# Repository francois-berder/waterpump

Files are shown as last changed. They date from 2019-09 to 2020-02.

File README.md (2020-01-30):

# Waterpump

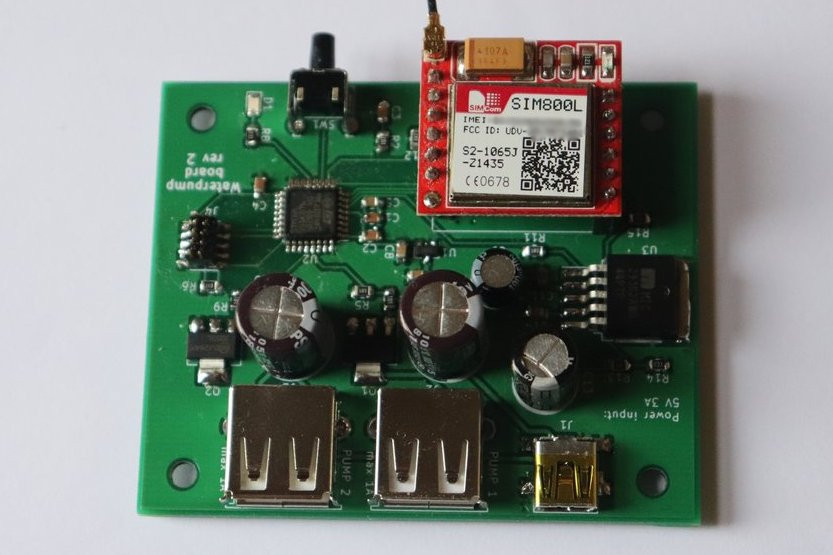
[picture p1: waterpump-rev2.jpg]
waterpump board Waterpump board rev 2


This project is an automatic system for watering plants. Everyday, pumps are switched on for a few seconds to provide enough water to some plants. The device can be controlled by sending SMS to change the schedule or water plants. In addition, a small push-button is present to water plants immediately.

## Build and flash instructions

### Prerequisites

You need to install the [ARM embedded toolchain](https://developer.arm.com/tools-and-software/open-source-software/developer-tools/gnu-toolchain/gnu-rm) and [JLink Software and Documentation Pack](https://www.segger.com/downloads/jlink/#J-LinkSoftwareAndDocumentationPack).

### SIM card configuration

The SIM card might need to be unlocked. The default PIN is set to 1234 by the `SIMCARD_PIN` macro that can be overriden.

To retrieve time from network, the firmware needs the APN name which depends on your
network provider. The macro `SIM800_APN_NAME` is currently set to `"free"` in the Makefile because I am using a SIM card from Free Mobile. Feel free to change it.

### Commands

There are two types of build: release and debug.

To build the project, run one of these commands:
```
$ make                  # BUILDTYPE set to release
$ BUILDTYPE=release make
$ BUILDTYPE=debug make
```

Connect the board to a SEGGER debug probe and run these commands to flash or debug the firmware:
```
$ make flash-target                 # Flash release firmware
$ BUILDTYPE=debug make flash-target # Flash debug firmware
$ BUILDTYPE=debug make debug-target # Start debugging firmware
```

## Building hardware

In `hardware` folder, there are Gerber files sent to [JLCPCB](https://jlcpcb.com/) for each revision of the board. I recommend that you build the latest revision of the board. Components can be bought on [RS online](https://uk.rs-online.com/web/).

### Issues with rev1 board

  * SIM800L Footprint is incorrect
  * No mounting holes
  * micro USB connector is too far away from the side of the board
  * Power circuit for SIM800L is not working properly. Large polarized capacitors are missing on the input and output of the LDO voltage regulator. The regulator is not able to handle load transients fast enough, causing the SIM800L to brown out.

### Issues with rev2 board

  * SIM800L footprint is still incorrect ! Although it is easier to insert the module in pin headers than on rev1.
  * micro USB connector should be replaced by a barrel connector because USB cables should not be used to provide 3A.

## Power requirements

The GSM module can use up to 2A and each pump should not use more than 1A due to the choice of MOSFET transistors (especially on rev 2).
For this reason, I recommend powering this board with a 5V 3A power supply. Alternatively if you are using only 2.5W pumps, a 5V 2.5A can be used.

## Switching on water pump

Both pumps are switched on in sequence for 3 seconds each if the push button is pressed or if the GSM modules receives a text message starting with "WATER ALL". If you only want to enable pump 1 or 2, send text message "WATER 1" or "WATER 2".

## SMS commands

| Command | description | examples |
| --- | --- | --- |
| `BUTTON <duration>` | Configure for how long each pump is enabled when button is pressed | `BUTTON 5` |
| `WATER <pump_index>` | Turn on one pump for `DEFAULT_PUMP_DURATION` seconds (default: 3s) | `WATER 1`, `WATER 2` |
| `WATER ALL` | Turn on both pumps, each for `DEFAULT_PUMP_DURATION` seconds (default: 3s)| `WATER ALL` |
| `SCHEDULE <index> STOP` | Disable a schedule| `SCHEDULE 0 STOP`, `SCHEDULE 1 STOP` |
| `SCHEDULE <index> <hour>:<min>:<sec> <duration> ALL` | Turn on both pumps once per day | `SCHEDULE 0 19:04:57 3 ALL` |
| `SCHEDULE <index> <hour>:<min>:<sec> <duration> <pump_index>` | Turn on a pump once per day | `SCHEDULE 2 06:43:00 7 1`, `SCHEDULE 3 06:43:00 9 2` |
| `SCHEDULE STATUS` | Request schedule status | `SCHEDULE STATUS` |

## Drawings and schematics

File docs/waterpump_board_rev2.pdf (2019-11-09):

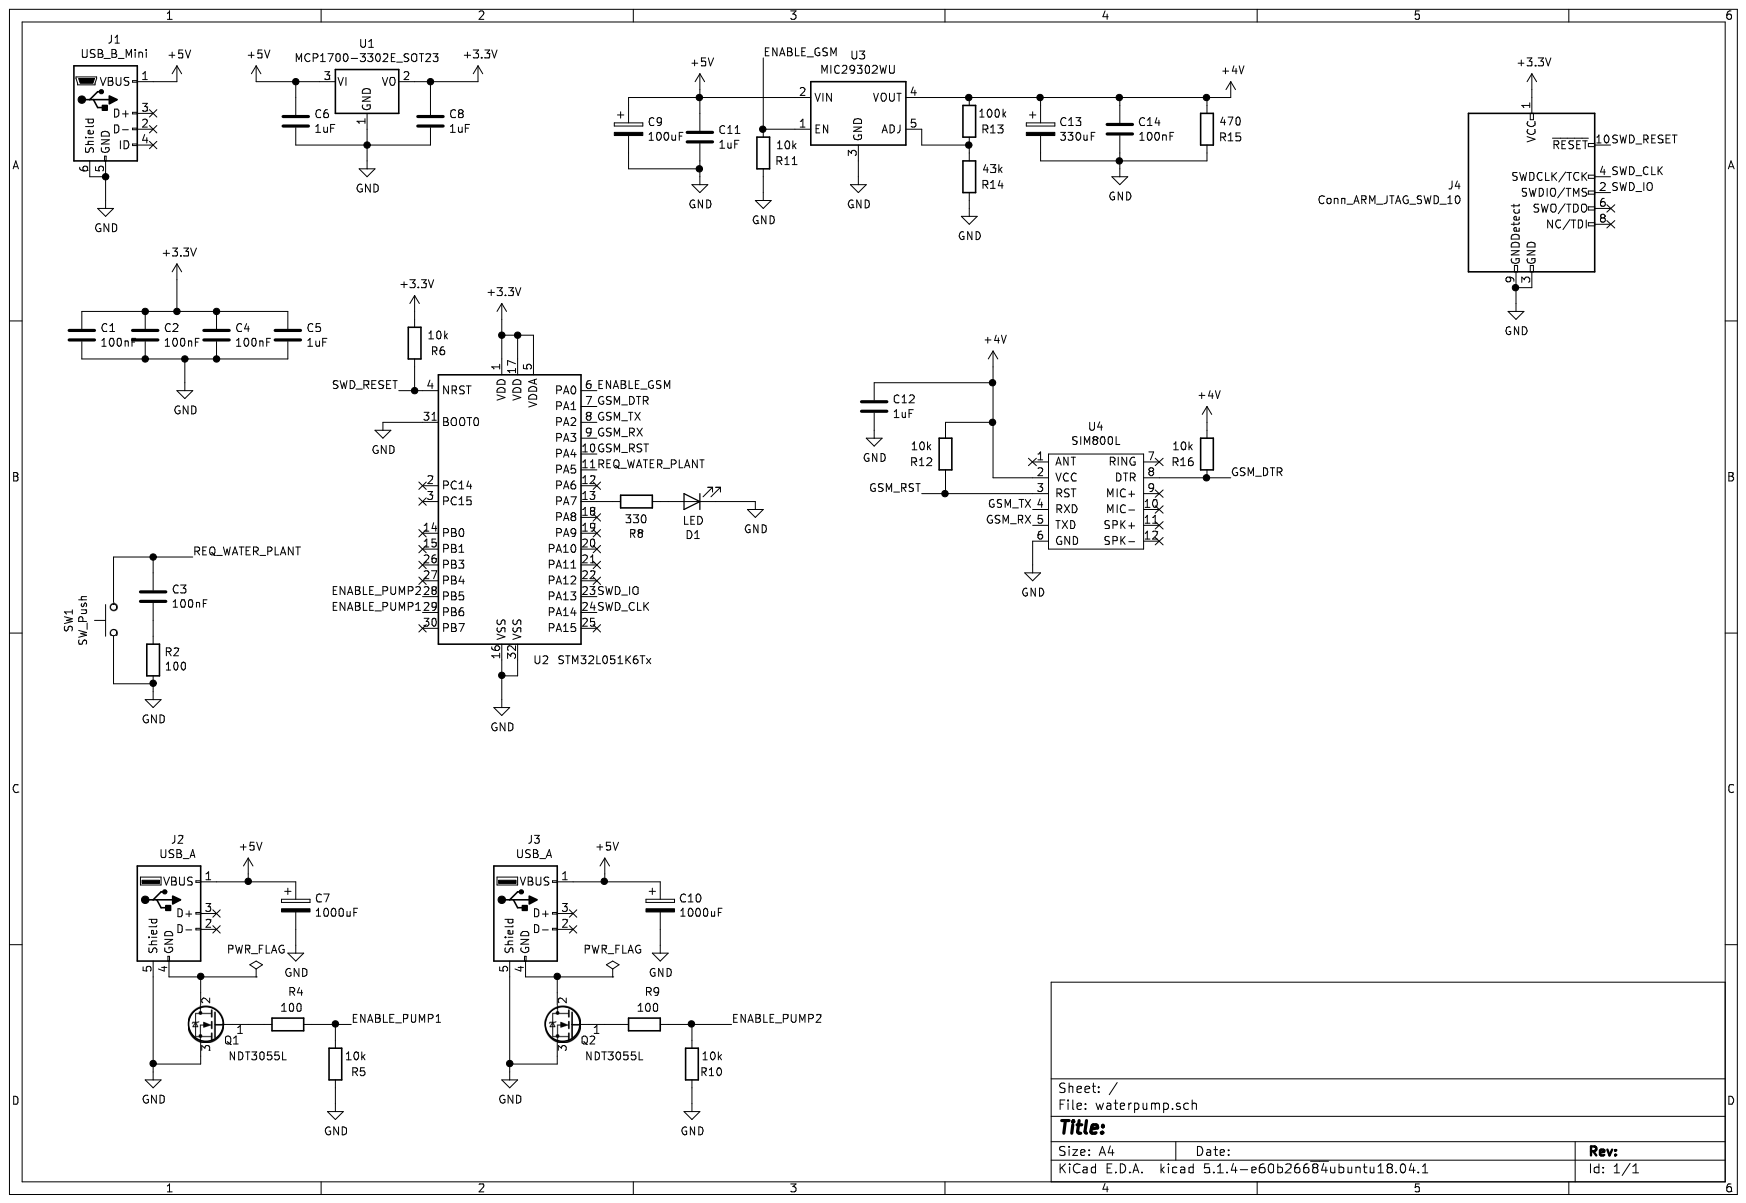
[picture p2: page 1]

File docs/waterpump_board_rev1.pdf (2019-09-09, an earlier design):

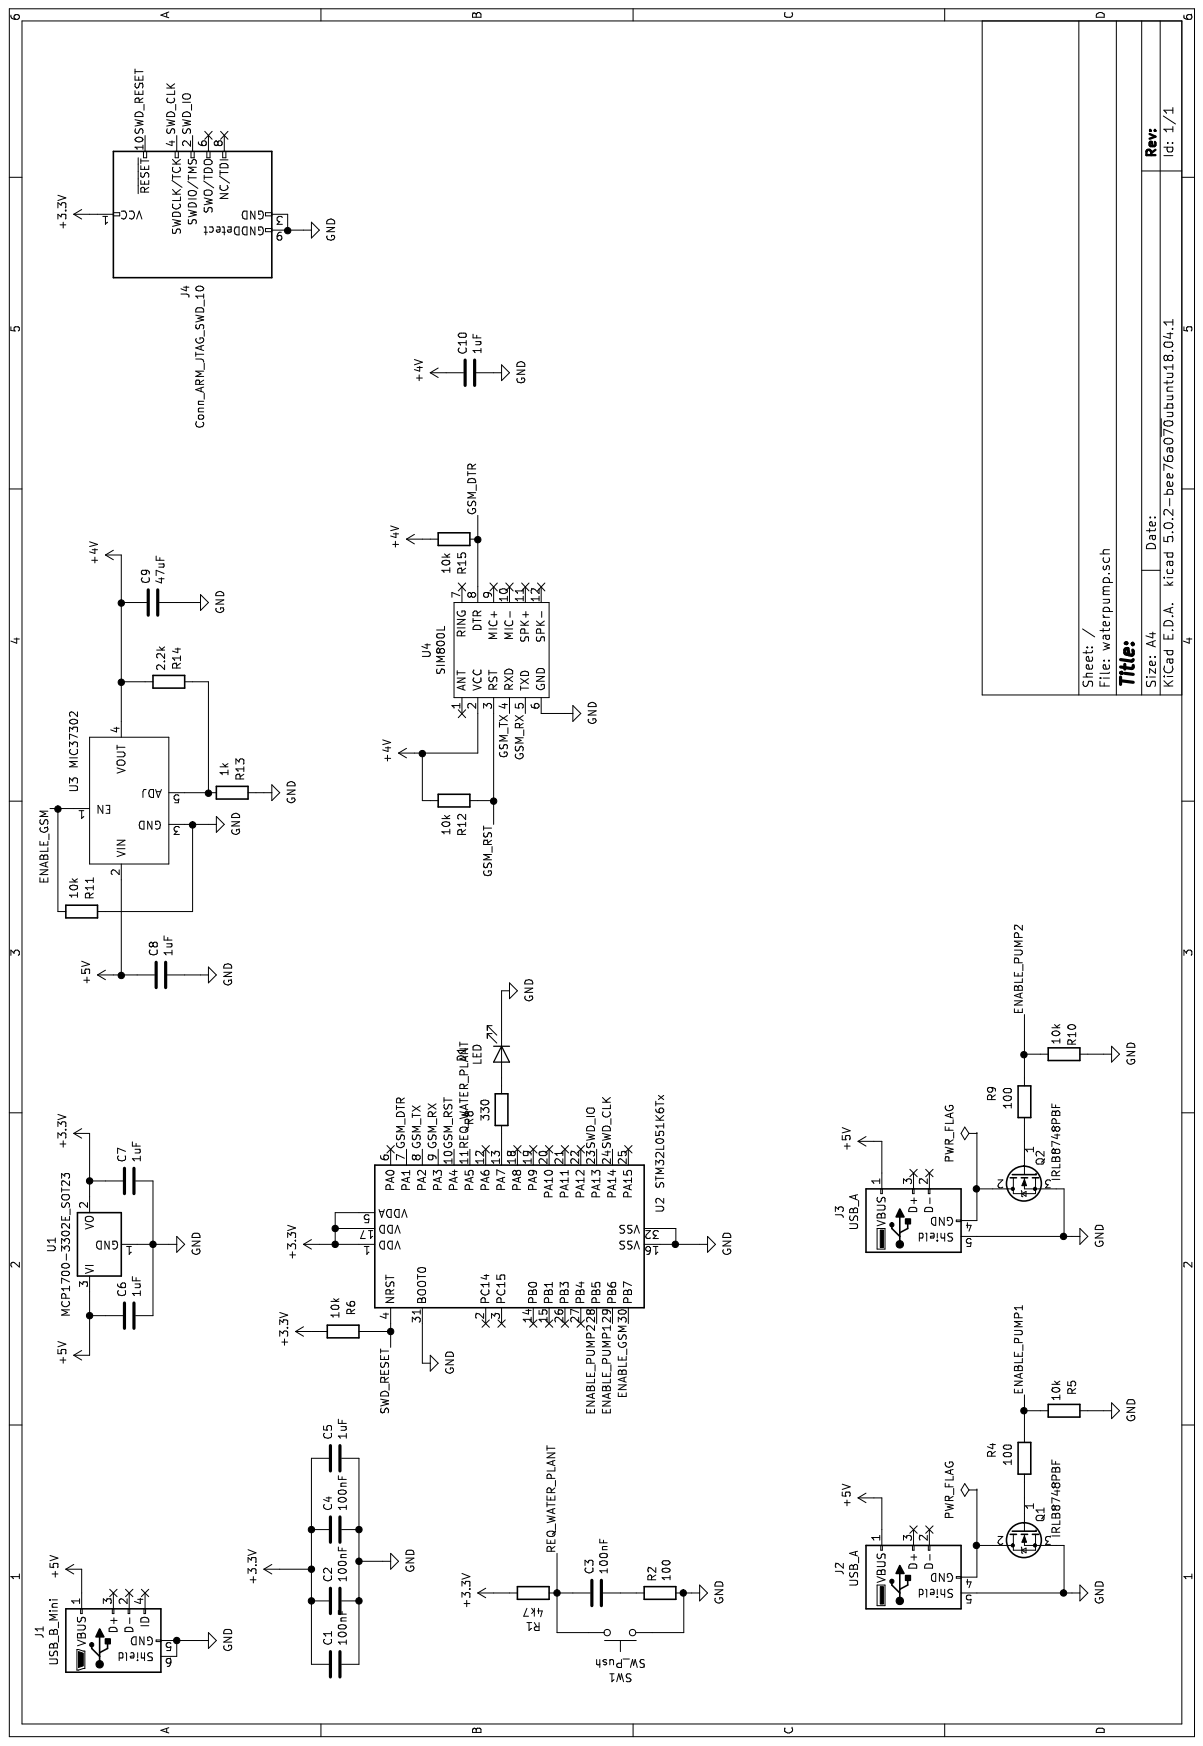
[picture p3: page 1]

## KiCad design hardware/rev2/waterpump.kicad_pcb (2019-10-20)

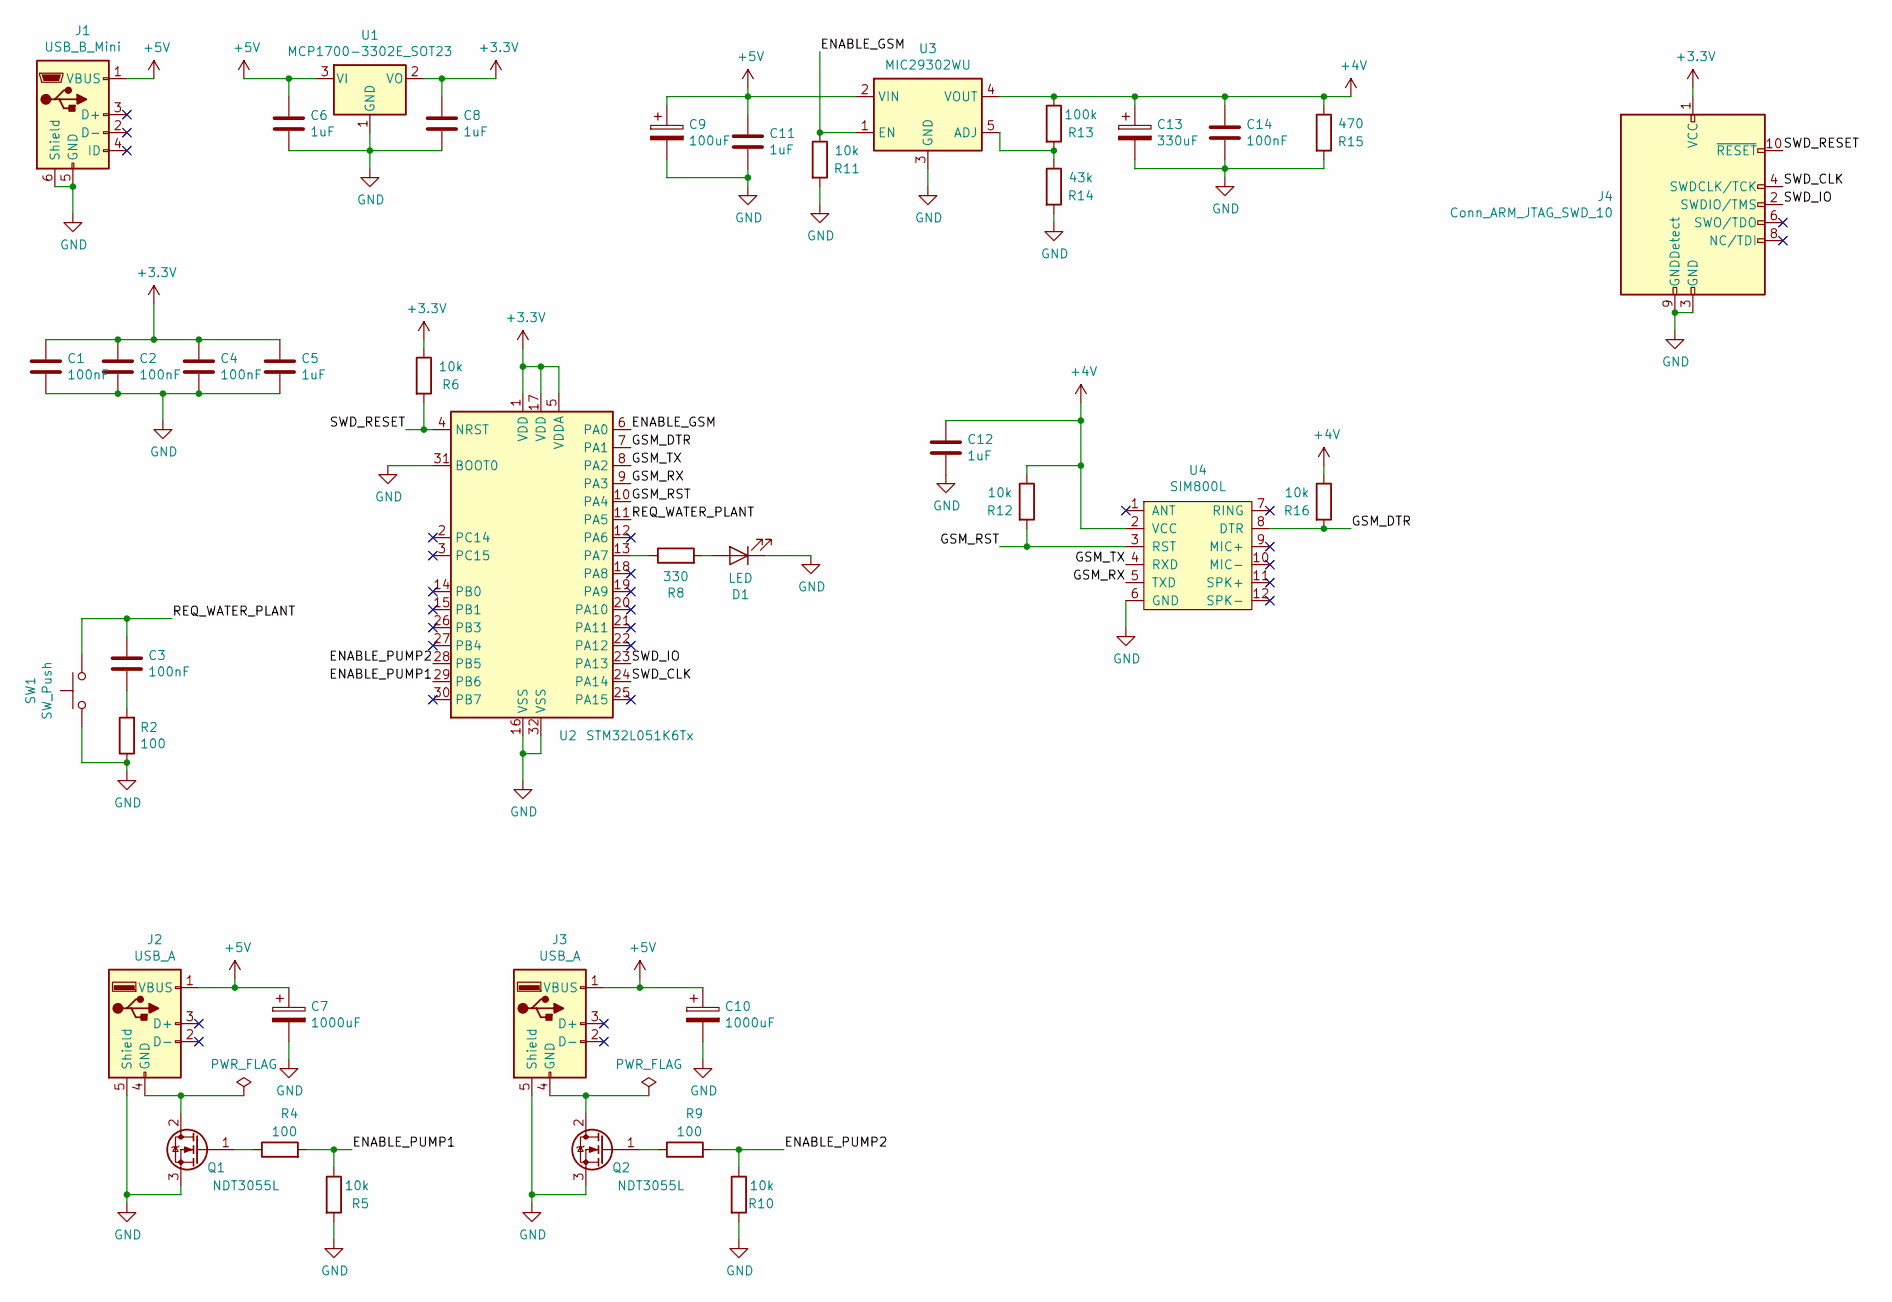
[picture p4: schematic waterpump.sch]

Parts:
C1, C2, C3, C4, C14: 100nF; C_0805_2012Metric
C5, C6, C8, C11, C12: 1uF; C_0805_2012Metric
C7, C10: 1000uF; CP_Radial_D10.0mm_P5.00mm
C9: 100uF; CP_Radial_D6.3mm_P2.50mm
C13: 330uF; CP_Radial_D8.0mm_P3.50mm
D1: LED; LED_0805_2012Metric
J1: USB_B_Mini; USB_Mini-B_Lumberg_2486_01_Horizontal
J2, J3: USB_A; USB_A_Stewart_SS-52100-001_Horizontal
J4: Conn_ARM_JTAG_SWD_10; PinHeader_2x05_P1.27mm_Vertical_SMD
Q1, Q2: NDT3055L; SOT-223-3_TabPin2
R2, R4, R9: 100; R_0805_2012Metric
R5, R6, R10, R11, R12, R16: 10k; R_0805_2012Metric
R8: 330; R_0805_2012Metric
R13: 100k; R_0805_2012Metric
R14: 43k; R_0805_2012Metric
R15: 470; R_0805_2012Metric
SW1: SW_Push; SW_Tactile_SKHH_Angled
U1: MCP1700-3302E_SOT23; SOT-23
U2: STM32L051K6Tx; LQFP-32_7x7mm_P0.8mm
U3: MIC29302WU; TO-263-5_TabPin3
U4: SIM800L

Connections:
+3V3: C1.1, C2.1, C4.1, C5.1, C8.1, J4.1 (VCC), R6.1, U1.2 (VO), U2.1 (VDD), U2.5 (VDDA), U2.17 (VDD)
+4V: C12.1, C13.1, C14.1, R12.1, R13.1, R15.1, R16.1, U3.4 (VOUT), U4.2 (VCC)
+5V: C6.1, C7.1, C9.1, C10.1, C11.1, J1.1 (VBUS), J2.1 (VBUS), J3.1 (VBUS), U1.3 (VI), U3.2 (VIN)
/ENABLE_GSM: R11.1, U2.6 (PA0), U3.1 (EN)
/ENABLE_PUMP1: R4.2, R5.1, U2.29 (PB6)
/ENABLE_PUMP2: R9.2, R10.1, U2.28 (PB5)
/GSM_DTR: R16.2, U2.7 (PA1), U4.8 (DTR)
/GSM_RST: R12.2, U2.10 (PA4), U4.3 (RST)
/GSM_RX: U2.9 (PA3), U4.5 (TXD)
/GSM_TX: U2.8 (PA2), U4.4 (RXD)
/REQ_WATER_PLANT: C3.1, SW1.2, U2.11 (PA5)
/SWD_CLK: J4.4 (SWDCLK/TCK), U2.24 (PA14)
/SWD_IO: J4.2 (SWDIO/TMS), U2.23 (PA13)
/SWD_RESET: J4.10 (~RESET~), R6.2, U2.4 (NRST)
GND: C1.2, C2.2, C4.2, C5.2, C6.2, C7.2, C8.2, C9.2, C10.2, C11.2, C12.2, C13.2, C14.2, D1.1 (K), J1.5 (GND), J1.6 (Shield), J2.5 (Shield), J3.5 (Shield), J4.3 (GND), J4.5 (GND), J4.9 (GNDDetect), Q1.3 (S), Q2.3 (S), R2.1, R5.2, R10.2, R11.2, R14.2, R15.2, SW1.1, U1.1 (GND), U2.16 (VSS), U2.31 (BOOT0), U2.32 (VSS), U3.3 (GND), U4.6 (GND)
unnamed: C3.2, R2.2
unnamed: D1.2 (A), R8.2
unnamed: J2.4 (GND), Q1.2 (D)
unnamed: J3.4 (GND), Q2.2 (D)
unnamed: Q1.1 (G), R4.1
unnamed: Q2.1 (G), R9.1
unnamed: R8.1, U2.13 (PA7)
unnamed: R13.2, R14.1, U3.5 (ADJ)

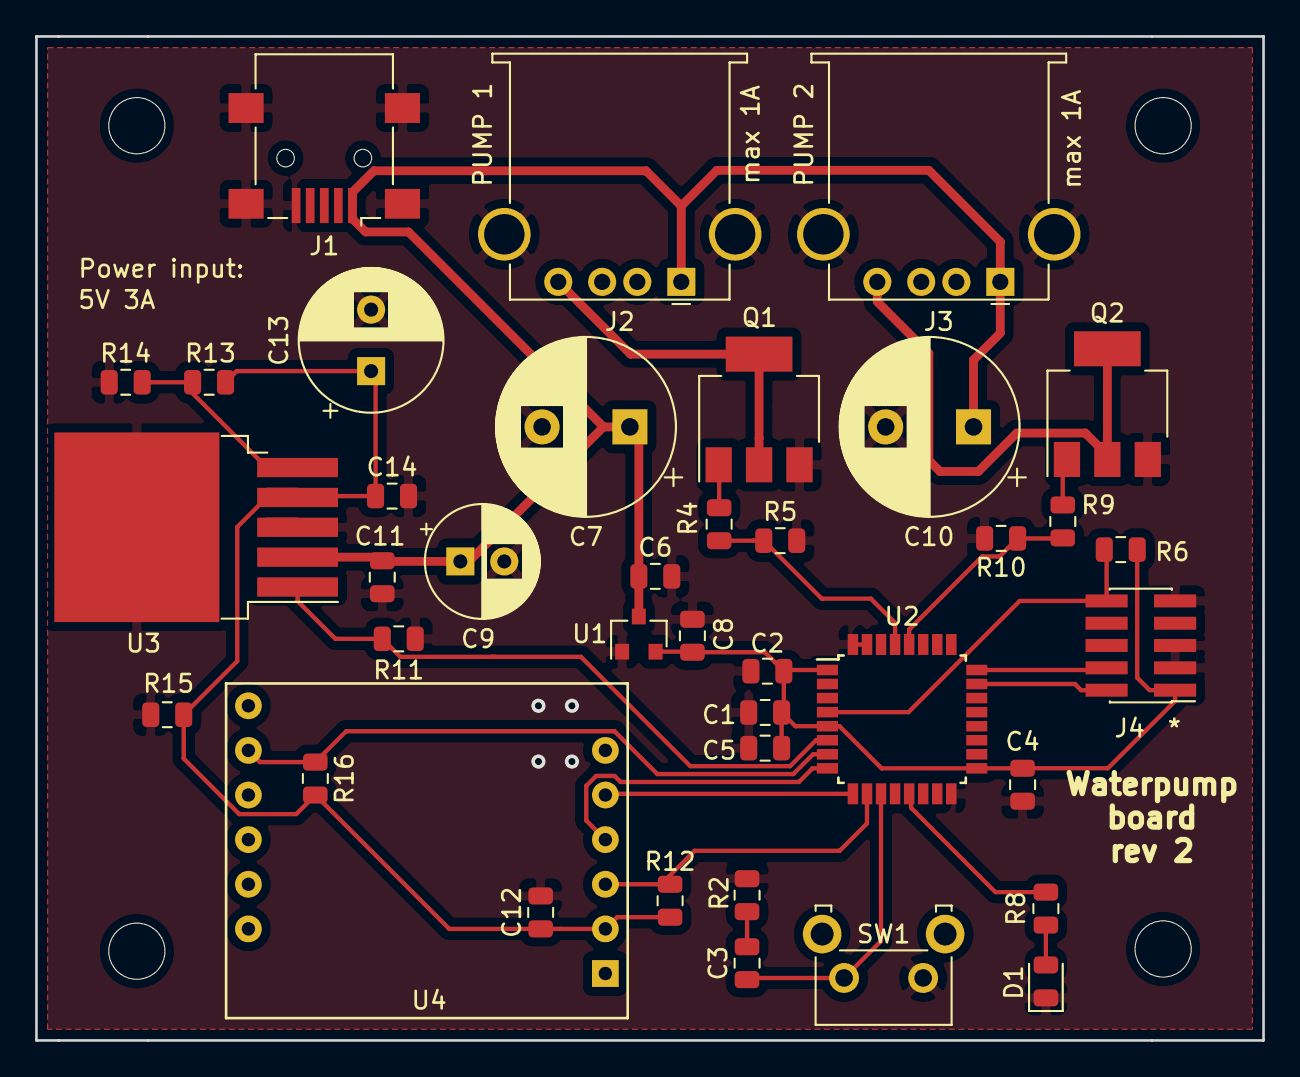
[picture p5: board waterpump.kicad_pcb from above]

Board: 2 copper layers, 69.8 x 57.2 mm, 39 parts (0 on the bottom side), 23 nets.

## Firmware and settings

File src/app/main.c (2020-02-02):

/*
 * Copyright (C) 2019 Francois Berder <fberder@outlook.fr>
 *
 * This file is part of waterpump.
 *
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
 * You should have received a copy of the GNU General Public License
 * along with waterpump.  If not, see <http://www.gnu.org/licenses/>.
 */

#include "app/board.h"
#include "app/pumps.h"
#include "app/schedule.h"
#include "app/sim800l.h"
#include "mcu/gpio.h"
#include "mcu/mcu.h"
#include "mcu/stm32l051xx.h"
#include "mcu/uart.h"
#include <ctype.h>
#include <stdlib.h>
#include <string.h>

#ifndef SIMCARD_PIN
#define SIMCARD_PIN     (1234)
#endif

#define GSM_ERROR_COUNTER_THRESHOLD     (10)

#ifndef DEFAULT_PUMP_DURATION
#define DEFAULT_PUMP_DURATION           (3)
#endif

static struct sim800l_params_t gsm_params = {
    .dev = SIM800_USART,
};
static uint32_t gsm_error_counter;
static int schedule_changed;
static int req_schedule_status;
static char req_schedule_number[22];

static uint8_t pump_duration = DEFAULT_PUMP_DURATION;

/* push button req water callback */
void ext5_callback(void)
{
    pumps_start(PUMP_ALL, pump_duration);
}

static void handle_sms(struct sim800l_sms_t *sms)
{
    uint8_t text_length = sms->text_length;
    char *text = sms->text;

    /* Remove leading whitespaces */
    while (text_length && text[0] == ' ') {
        text_length--;
        text++;
    }

    if (text_length < 9)
        return;

    if (text_length >= 11 && !strncmp(text, "WATER ALL\r\n", 11))
        pumps_start(PUMP_ALL, DEFAULT_PUMP_DURATION);
    else if (!strncmp(text, "WATER 1\r\n", 9))
        pumps_start(PUMP_1, DEFAULT_PUMP_DURATION);
    else if (!strncmp(text, "WATER 2\r\n", 9))
        pumps_start(PUMP_2, DEFAULT_PUMP_DURATION);
    else if (!strncmp(text, "BUTTON ", 7)) {
        if (text_length == 8 && isdigit(text[7]))
            pump_duration = text[7] - '0';
        else if (text_length == 9
             && isdigit(text[7])
             && isdigit(text[8]))
            pump_duration = (text[7] - '0') * 10 + (text[8] - '0');
    } else if (!strncmp(text, "SCHEDULE 0 STOP\r\n", 17)) {
        schedule_disable(0);
        schedule_changed = 1;
    } else if (!strncmp(text, "SCHEDULE 1 STOP\r\n", 17)) {
        schedule_disable(1);
        schedule_changed = 1;
    } else if (!strncmp(text, "SCHEDULE 2 STOP\r\n", 17)) {
        schedule_disable(2);
        schedule_changed = 1;
    } else if (!strncmp(text, "SCHEDULE 3 STOP\r\n", 17)) {
        schedule_disable(3);
        schedule_changed = 1;
    } else if (!strncmp(text, "SCHEDULE 4 STOP\r\n", 17)) {
        schedule_disable(4);
        schedule_changed = 1;
    } else if (!strncmp(text, "SCHEDULE STATUS\r\n", 17)) {
        req_schedule_status = 1;
        strcpy(req_schedule_number, sms->header.sender);
    } else if (text_length >= 23 && !strncmp(text, "SCHEDULE ", 9)) {
        uint8_t index;
        uint8_t hour, min, sec;
        enum pump_t pumps;
        uint8_t duration;
        char *ptr;

        if (!isdigit(text[9])
        ||  text[10] != ' '
        ||  !isdigit(text[11])
        ||  !isdigit(text[12])
        ||  text[13] != ':'
        ||  !isdigit(text[14])
        ||  !isdigit(text[15])
        ||  text[16] != ':'
        ||  !isdigit(text[17])
        ||  !isdigit(text[18])
        ||  text[19] != ' '
        ||  !isdigit(text[20]))
            return;

        index = text[9] - '0';
        if (index >= SCHEDULE_COUNT)
            return;

        hour = (text[11] - '0') * 10 + (text[12] - '0');
        if (hour > 23)
            return;

        min = (text[14] - '0') * 10 + (text[15] - '0');
        if (min > 59)
            return;

        sec = (text[17] - '0') * 10 + (text[18] - '0');
        if (sec > 59)
            return;

        duration = (text[20] - '0');
        ptr = &text[21];
        if (isdigit(*ptr))
            duration = (duration * 10) + (*ptr++ - '0');

        if (*ptr++ != ' ')
            return;

        if (*ptr == '1')
            pumps = PUMP_1;
        else if (*ptr == '2')
            pumps = PUMP_2;
        else if (text_length >= 25
              && ptr[0] == 'A'
              && ptr[1] == 'L'
              && ptr[2] == 'L')
            pumps = PUMP_ALL;
        else
            return;

        schedule_configure(index, hour, min, sec, pumps, duration);
        schedule_changed = 1;
    }
}

static int gsm_init(void)
{
    enum sim800l_sim_status_t sim_status;

    if (sim800l_enable_time_update_from_network(&gsm_params))
        return -1;

    if (sim800l_check_sim_card_present(&gsm_params)
    ||  sim800l_get_sim_status(&gsm_params, &sim_status))
        return -1;

    if (sim_status == SIM_PIN_LOCK) {
        if (sim800l_unlock_sim(&gsm_params, SIMCARD_PIN))
            return -1;

        /* Give it a bit of time to unlock SIM card */
        mcu_delay(5000);

        if (sim800l_get_sim_status(&gsm_params, &sim_status))
            return -1;
        if (sim_status != SIM_READY)
            return -1;
    } else if (sim_status != SIM_READY) {
        return -1;
    }

    if (sim800l_set_sms_format_to_text(&gsm_params))
        return -1;

    /* Wait for SIM card to become "SMS READY" */
    mcu_delay(5000);

    if (sim800l_use_simcard_for_sms_storage(&gsm_params)
    ||  sim800l_delete_all_sms(&gsm_params))
        return -1;

    /* Retrieve time from network */
    if (sim800l_sync_time(&gsm_params))
        return -1;

    return 0;
}

static int gsm_update(void)
{
    enum sim800l_network_registration_status_t status;

    if (sim800l_check_network_registration(&gsm_params, &status))
        return -1;

    if (status == SIM800_NOT_REGISTERED) {
        if (sim800l_connect_to_network(&gsm_params))
            return -1;
    }

    req_schedule_status = 0;
    if (sim800l_read_all_unread_sms(&gsm_params, handle_sms))
        return -1;

    if (req_schedule_status) {
        char buf[128];
        schedule_to_string(buf);
        sim800l_send_sms(&gsm_params, req_schedule_number, buf);
        req_schedule_status = 0;
    }

    return 0;
}

int main(void)
{
    int gsm_enabled = 0;

    /* Set core clock to 4.2MHz */
    RCC->ICSCR = (RCC->ICSCR & ~RCC_ICSCR_MSIRANGE) | RCC_ICSCR_MSIRANGE_6;

    /* Set Vcore to 1.2V */
    RCC->APB1ENR |= RCC_APB1ENR_PWREN;
    PWR->CR |= PWR_CR_VOS_0 | PWR_CR_VOS_1;
    while (PWR->CSR & PWR_CSR_VOSF);

    /* Initialize GPIOs */
    gpio_init_out(LED_PIN, 0);
    gpio_init_out(ENABLE_GSM_PIN, 0);
    gpio_init_out(ENABLE_PUMP1_PIN, 0);
    gpio_init_out(ENABLE_PUMP2_PIN, 0);
    gpio_init_int(REQ_WATER_PIN, PULL_UP, GPIO_FALLING);
    gpio_init_out(GSM_TX_PIN, 1);
    gpio_init_in(GSM_RX_PIN, PULL_UP);
    gpio_init_af(GSM_TX_PIN, 4);
    gpio_init_af(GSM_RX_PIN, 4);

    uart_power_up(USART2);
    uart_set_rx_callback(USART2, sim800l_receive_cb);
    uart_init(USART2, 115200);
    uart_enable(USART2);

    /* Configure NVIC and enable interrupts */
    NVIC_EnableIRQ(EXTI4_15_IRQn);
    NVIC_EnableIRQ(TIM2_IRQn);
    NVIC_EnableIRQ(TIM21_IRQn);
    NVIC_EnableIRQ(TIM22_IRQn);
    NVIC_EnableIRQ(USART2_IRQn);
    NVIC_EnableIRQ(RTC_IRQn);
    __enable_irq();

    /*
     * Ensure that SIM800 is initialized with a correct time
     * before initializing schedule.
     */
    while (1) {
        /* 1. Power up 2G module */
        gpio_write(ENABLE_GSM_PIN, 1);
        gsm_enabled = 1;

        mcu_delay(5000);

        /* Initialize SIM800 module */
        if (!gsm_init())
            break;

        /* Power down 2G module for a little while */
        gpio_write(ENABLE_GSM_PIN, 0);
        gsm_enabled = 0;
        mcu_delay(10000);
    }

    schedule_init();

    while (1) {
        __asm__ volatile ("wfi" ::: "memory");

        /*
         * If SIM800L waked us, let's wait it sent everything
         * before we attempt to read from UART
         */
        mcu_delay(20);

        if (!gsm_enabled)
            continue;

        if (gsm_update()) {
            gsm_error_counter++;
            if (gsm_error_counter > GSM_ERROR_COUNTER_THRESHOLD) {
                gpio_write(ENABLE_GSM_PIN, 0);
                gsm_enabled = 0;
            }
        } else {
            if (schedule_changed)
                schedule_apply_configuration();
            gsm_error_counter = 0;
            schedule_changed = 0;
        }
    }

    __builtin_unreachable();
}

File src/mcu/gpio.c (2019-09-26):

/*
 * Copyright (C) 2019 Francois Berder <fberder@outlook.fr>
 *
 * This file is part of waterpump.
 *
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
 * You should have received a copy of the GNU General Public License
 * along with waterpump.  If not, see <http://www.gnu.org/licenses/>.
 */

#include "mcu/gpio.h"
#include "mcu/stm32l051xx.h"
#include <stdint.h>

#define GPIO_PORT(PIN)      (((PIN) >> 4) & 0xF)
#define GPIO_IDX(PIN)       ((PIN) & 0xF)

static GPIO_TypeDef* const base_address[PORT_COUNT] = {
    GPIOA,
    GPIOB,
    GPIOC,
    GPIOD,
    GPIOH,
};

static void dummy_ext_callback(void)
{

}

void __attribute__((weak, alias("dummy_ext_callback"))) ext0_callback(void);
void __attribute__((weak, alias("dummy_ext_callback"))) ext1_callback(void);
void __attribute__((weak, alias("dummy_ext_callback"))) ext2_callback(void);
void __attribute__((weak, alias("dummy_ext_callback"))) ext3_callback(void);
void __attribute__((weak, alias("dummy_ext_callback"))) ext4_callback(void);
void __attribute__((weak, alias("dummy_ext_callback"))) ext5_callback(void);
void __attribute__((weak, alias("dummy_ext_callback"))) ext6_callback(void);
void __attribute__((weak, alias("dummy_ext_callback"))) ext7_callback(void);
void __attribute__((weak, alias("dummy_ext_callback"))) ext8_callback(void);
void __attribute__((weak, alias("dummy_ext_callback"))) ext9_callback(void);
void __attribute__((weak, alias("dummy_ext_callback"))) ext10_callback(void);
void __attribute__((weak, alias("dummy_ext_callback"))) ext11_callback(void);
void __attribute__((weak, alias("dummy_ext_callback"))) ext12_callback(void);
void __attribute__((weak, alias("dummy_ext_callback"))) ext13_callback(void);
void __attribute__((weak, alias("dummy_ext_callback"))) ext14_callback(void);
void __attribute__((weak, alias("dummy_ext_callback"))) ext15_callback(void);

void exti0_1_isr_handler(void)
{
    if (EXTI->PR & (1U << 0)) { ext0_callback(); EXTI->PR |= 1U << 0; }
    if (EXTI->PR & (1U << 1)) { ext1_callback(); EXTI->PR |= 1U << 1; }
}

void exti2_3_isr_handler(void)
{
    if (EXTI->PR & (1U << 2)) { ext2_callback(); EXTI->PR |= 1U << 2; }
    if (EXTI->PR & (1U << 3)) { ext3_callback(); EXTI->PR |= 1U << 3; }
}

void exti4_15_isr_handler(void)
{
    if (EXTI->PR & (1U << 4)) { ext4_callback(); EXTI->PR |= 1U << 4; }
    if (EXTI->PR & (1U << 5)) { ext5_callback(); EXTI->PR |= 1U << 5; }
    if (EXTI->PR & (1U << 6)) { ext6_callback(); EXTI->PR |= 1U << 6; }
    if (EXTI->PR & (1U << 7)) { ext7_callback(); EXTI->PR |= 1U << 7; }
    if (EXTI->PR & (1U << 8)) { ext8_callback(); EXTI->PR |= 1U << 8; }
    if (EXTI->PR & (1U << 9)) { ext9_callback(); EXTI->PR |= 1U << 9; }
    if (EXTI->PR & (1U << 10)) { ext10_callback(); EXTI->PR |= 1U << 10; }
    if (EXTI->PR & (1U << 11)) { ext11_callback(); EXTI->PR |= 1U << 11; }
    if (EXTI->PR & (1U << 12)) { ext12_callback(); EXTI->PR |= 1U << 12; }
    if (EXTI->PR & (1U << 13)) { ext13_callback(); EXTI->PR |= 1U << 13; }
    if (EXTI->PR & (1U << 14)) { ext14_callback(); EXTI->PR |= 1U << 14; }
    if (EXTI->PR & (1U << 15)) { ext15_callback(); EXTI->PR |= 1U << 15; }
}

static void configure_pull_up_down(GPIO_TypeDef * const regs, uint32_t index, enum pull_mode_t mode)
{
    regs->PUPDR &= ~(0x3U << (2 * index));
    switch (mode) {
    case PULL_UP:
        regs->PUPDR |= 0x1U << (2 * index);
        break;
    case PULL_DOWN:
        regs->PUPDR |= 0x2U << (2 * index);
        break;
    default:
        break;
    }
}

void gpio_init_out(uint8_t gpio, int val)
{
    uint32_t port = GPIO_PORT(gpio);
    uint32_t index = GPIO_IDX(gpio);
    GPIO_TypeDef * const regs = base_address[port];

    RCC->IOPENR |= RCC_IOPENR_GPIOAEN << port;

    configure_pull_up_down(regs, index, PULL_NONE);
    if (val)
        regs->BSRR |= 0x1U << index;
    else
        regs->BRR |= 0x1U << index;

    regs->MODER &= ~(0x3U << (2 * index));
    regs->OTYPER &= ~(0x1U << index);
    regs->OSPEEDR &= ~(0x3U << (2 * index));    /* slow speed */
    regs->MODER |= 0x1U << (2 * index);
}

void gpio_init_od(uint8_t gpio, enum pull_mode_t mode, int val)
{
    uint32_t port = GPIO_PORT(gpio);
    uint32_t index = GPIO_IDX(gpio);
    GPIO_TypeDef * const regs = base_address[port];

    RCC->IOPENR |= RCC_IOPENR_GPIOAEN << port;

    configure_pull_up_down(regs, index, mode);
    if (val)
        regs->BSRR |= 0x1U << index;
    else
        regs->BRR |= 0x1U << index;

    regs->MODER &= ~(0x3U << (2 * index));
    regs->OTYPER &= ~(0x1U << index);
    regs->OSPEEDR &= ~(0x3U << (2 * index));    /* slow speed */
    regs->OTYPER |= 0x1U << index;
    regs->MODER |= 0x1U << (2 * index);
}

void gpio_init_in(uint8_t gpio, enum pull_mode_t mode)
{
    uint32_t port = GPIO_PORT(gpio);
    uint32_t index = GPIO_IDX(gpio);
    GPIO_TypeDef * const regs = base_address[port];

    RCC->IOPENR |= RCC_IOPENR_GPIOAEN << port;

    configure_pull_up_down(regs, index, mode);

    regs->MODER &= ~(0x3U << (2 * index));
}
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

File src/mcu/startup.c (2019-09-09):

/*
 * Copyright (C) 2019 Francois Berder <fberder@outlook.fr>
 *
 * This file is part of waterpump.
 *
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
 * You should have received a copy of the GNU General Public License
 * along with waterpump.  If not, see <http://www.gnu.org/licenses/>.
 */

#include "stm32l051xx.h"
#include <stdint.h>

extern uint32_t _end_stack;
extern uint32_t _end_text;
extern uint32_t _start_data;
extern uint32_t _end_data;
extern uint32_t _start_bss;
extern uint32_t _end_bss;

int main(void);

void reset_handler(void)
{
    register uint32_t *src, *dst;

    /* Copy data section from flash to RAM */
    src = &_end_text;
    dst = &_start_data;
    while (dst < &_end_data)
        *dst++ = *src++;

    /* Clear the bss section, assumes .bss goes directly after .data */
    dst = &_start_bss;
    while (dst < &_end_bss)
        *dst++ = 0;

    main();

    __disable_irq();
    while (1);
}

void default_handler(void)
{
    __disable_irq();
    while (1);
}

void nmi_handler(void) __attribute__((weak, alias("default_handler")));
void hardfault_handler(void) __attribute__((weak, alias("default_handler")));
void svcall_handler(void) __attribute__((weak, alias("default_handler")));
void pendsv_handler(void) __attribute__((weak, alias("default_handler")));
void systick_handler(void) __attribute__((weak, alias("default_handler")));

void * const core_vector_table[16] __attribute__ ((section(".cortex_vectors"))) = {
    [0] = &_end_stack,
    [1] = reset_handler,
    [2] = nmi_handler,
    [3] = hardfault_handler,
    [11] = svcall_handler,
    [14] = pendsv_handler,
    [15] = systick_handler,
};

void wwdg_isr_handler(void) __attribute__((weak, alias("default_handler")));
void pvd_isr_handler(void) __attribute__((weak, alias("default_handler")));
void rtc_isr_handler(void) __attribute__((weak, alias("default_handler")));
void flash_isr_handler(void) __attribute__((weak, alias("default_handler")));
void rcc_isr_handler(void) __attribute__((weak, alias("default_handler")));
void exti0_1_isr_handler(void) __attribute__((weak, alias("default_handler")));
void exti2_3_isr_handler(void) __attribute__((weak, alias("default_handler")));
void exti4_15_isr_handler(void) __attribute__((weak, alias("default_handler")));
void dma1_channel1_isr_handler(void) __attribute__((weak, alias("default_handler")));
void dma1_channel2_3_isr_handler(void) __attribute__((weak, alias("default_handler")));
void dma1_channel4_5_6_7_isr_handler(void) __attribute__((weak, alias("default_handler")));
void adc1_comp_isr_handler(void) __attribute__((weak, alias("default_handler")));
void lptim1_isr_handler(void) __attribute__((weak, alias("default_handler")));
void tim2_isr_handler(void) __attribute__((weak, alias("default_handler")));
void tim6_isr_handler(void) __attribute__((weak, alias("default_handler")));
void tim21_isr_handler(void) __attribute__((weak, alias("default_handler")));
void tim22_isr_handler(void) __attribute__((weak, alias("default_handler")));
void i2c1_isr_handler(void) __attribute__((weak, alias("default_handler")));
void i2c2_isr_handler(void) __attribute__((weak, alias("default_handler")));
void spi1_isr_handler(void) __attribute__((weak, alias("default_handler")));
void spi2_isr_handler(void) __attribute__((weak, alias("default_handler")));
void usart1_isr_handler(void) __attribute__((weak, alias("default_handler")));
void usart2_isr_handler(void) __attribute__((weak, alias("default_handler")));
void lpuart1_isr_handler(void) __attribute__((weak, alias("default_handler")));

void * const isr_vector_table[] __attribute__ ((section(".vendor_vectors"))) = {
    [WWDG_IRQn]                       = wwdg_isr_handler,
    [PVD_IRQn]                        = pvd_isr_handler,
    [RTC_IRQn]                        = rtc_isr_handler,
    [FLASH_IRQn]                      = flash_isr_handler,
    [RCC_IRQn]                        = rcc_isr_handler,
    [EXTI0_1_IRQn]                    = exti0_1_isr_handler,
    [EXTI2_3_IRQn]                    = exti2_3_isr_handler,
    [EXTI4_15_IRQn]                   = exti4_15_isr_handler,
    [DMA1_Channel1_IRQn]              = dma1_channel1_isr_handler,
    [DMA1_Channel2_3_IRQn]            = dma1_channel2_3_isr_handler,
    [DMA1_Channel4_5_6_7_IRQn]        = dma1_channel4_5_6_7_isr_handler,
    [ADC1_COMP_IRQn]                  = adc1_comp_isr_handler,
    [LPTIM1_IRQn]                     = lptim1_isr_handler,
    [TIM2_IRQn]                       = tim2_isr_handler,
    [TIM6_IRQn]                       = tim6_isr_handler,
    [TIM21_IRQn]                      = tim21_isr_handler,
    [TIM22_IRQn]                      = tim22_isr_handler,
    [I2C1_IRQn]                       = i2c1_isr_handler,
    [I2C2_IRQn]                       = i2c2_isr_handler,
    [SPI1_IRQn]                       = spi1_isr_handler,
    [SPI2_IRQn]                       = spi2_isr_handler,
    [USART1_IRQn]                     = usart1_isr_handler,
    [USART2_IRQn]                     = usart2_isr_handler,
    [LPUART1_IRQn]                    = lpuart1_isr_handler,
};

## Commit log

2019-09-12 Implement RTC wake up timer driver
2019-09-12 Do not enable NVIC interrupt in GPIO driver
2019-09-12 Move pins definitions to board.h
    Also define clock speeds
2019-09-26 tools: Use SWD to communicate with the ARM core
2019-09-26 Configure interrupt and callback for req water button
2019-09-26 Implement timer HAL
2019-09-26 Enable pumps for 3 second when button is pressed
2019-09-28 docs: Rename stm32l051k6 datasheet
2019-09-28 docs: Add stm32l051xx reference manual
2019-09-28 Implement UART HAL
2019-10-02 Implement uart_receive_noblock
2019-10-03 Replace uart_receive_noblock by UART RX INT
    [uart.c]
2019-10-05 fixup! Refactor gsm initialization
    [main.c]
2019-10-06 Fix timer 21/22 interrupt handler
    [timer.c]
2019-10-08 Enable pumps when receiving SMS
    SMS text must start with "REQ WATER" to enable the pumps.
2019-10-08 Make sure that all characters are sent before leaving uart_send
2019-10-12 Return correct status if SIM800L is looking for network
    [sim800l.c]
2019-10-15 Fix initialization of GSM module
    [main.c]
2019-10-17 hardware: Add rev1 Kicad files
    [waterpump.kicad_pcb, waterpump.sch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]
2019-10-17 fixup! hardware: Add rev1 factory files
    [waterpump_alt-B.Cu.gbr, waterpump_alt-B.Mask.gbr, waterpump_alt-B.Paste.gbr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]
2019-10-20 hardware: Add Kicad files for rev2 board
    [waterpump.kicad_pcb, waterpump.sch]
2019-10-20 hardware: Add files for rev2 board sent to factory
2019-10-20 Enable pumps in sequence
    Both pumps and GSM cannot be all on at the same time
    as they might use too much power.
    [pumps.c]
2019-10-20 readme: Add info about power requirements and how to switch on the pump
2019-10-28 Ensure pump 2 is off for a second before stopping pumps module
2019-10-28 Enhance pumps module to enable only one pump
2019-11-09 Allow starting only one pump via SMS
2019-11-09 readme: Update text message to enable pumps
2019-11-09 docs: Add schematics for rev2
2019-11-09 Change ENABLE_GSM pin for rev2 board
2019-11-09 Fix length check in handle_sms
    [main.c]
2019-11-09 Use internal pull-up on REQ_WATER pin
2019-11-09 readme: Add rev2 board issues
2019-11-16 Disable GSM after 10 consecutive errors
    [main.c]
2019-11-16 Revert "Implement RTC wake up timer driver"
    This reverts commit e43a198a27f5da32a88bd026057ed1c3d6771577.
2019-11-16 readme: Add rev 2 board image
2019-11-16 mcu: Fix TIM22 driver
    [timer.c]
2019-11-16 app: Blink LED while pumps are enabled
2019-11-17 mcu: Implement eeprom driver
2019-12-17 readme: Add issue about power connector on rev2 board
2020-01-05 Fix parsing SIM800 RTC time
    [sim800l.c]
2020-01-07 app: Allow turning on pumps for a variable amount of time
2020-01-07 readme: Mention how to change default SIM card PIN
2020-01-07 app: Do not show time, pump if schedule is off
2020-01-07 app: Print duration in schedule_to_string
2020-01-16 app: Calibrate LSI clock
2020-01-29 Reduce Vcore to 1.2V
2020-01-29 Turn off LED by default
2020-01-30 Configure pump duration if buttton pressed
2020-01-30 readme: Document BUTTON command
2020-02-02 Fix parsing SCHEDULE command
    [main.c]

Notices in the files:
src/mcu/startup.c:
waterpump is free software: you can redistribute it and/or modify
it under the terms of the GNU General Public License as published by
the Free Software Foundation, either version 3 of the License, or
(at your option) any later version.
